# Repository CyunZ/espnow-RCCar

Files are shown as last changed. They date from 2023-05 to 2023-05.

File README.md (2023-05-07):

# espnow-RCCar
用espnow通讯的遥控车

### 额外物料
ESP32开发板 2个  
MG996R舵机 1个  
130高扭矩电机（附赠8齿齿轮） 1个  
蓝丁胶  
按钮 4个  
686ZZ轴承（6*13*5） 至少4只  
TLP281光耦模块 1个  
L298N电机驱动模块 1个  
DCDC模块 若干 （3.3V给单片机供电，5V给舵机、电机供电 ，可以拆废旧充电宝的模块代替）  
18650电池+电池盒 若干（1个DCDC模块至少需要2节电池，充电宝模块只需要1节）  
M2螺丝 若干（固定开发板用，可以用蓝丁胶代替）  
M3螺丝+螺母 若干  
洞洞板、排针、排母（非必须，减少杜邦线的使用，简洁一点而已）  
杜邦线 若干  

### 视频地址
https://www.bilibili.com/video/BV1cz4y1a7o8

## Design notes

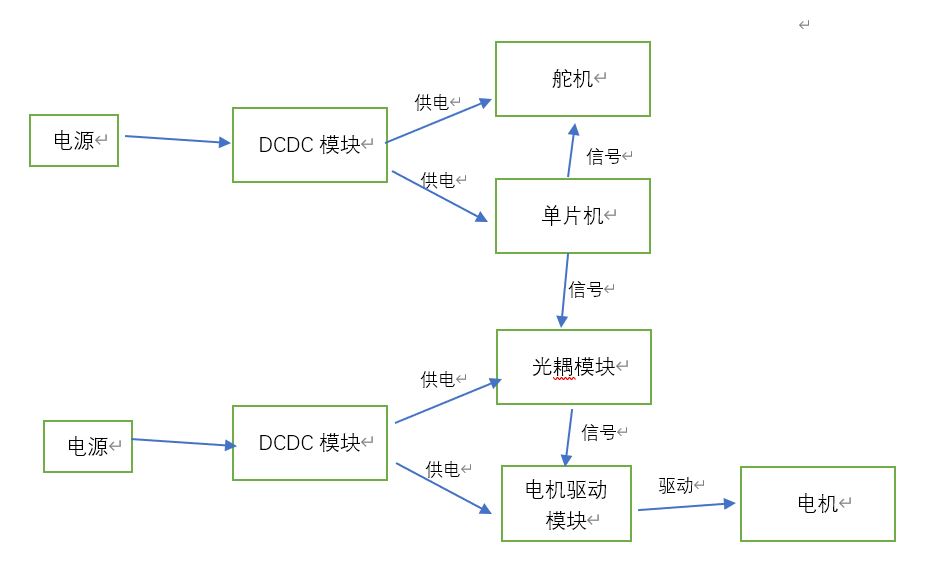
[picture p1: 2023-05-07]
接线示意图.JPG

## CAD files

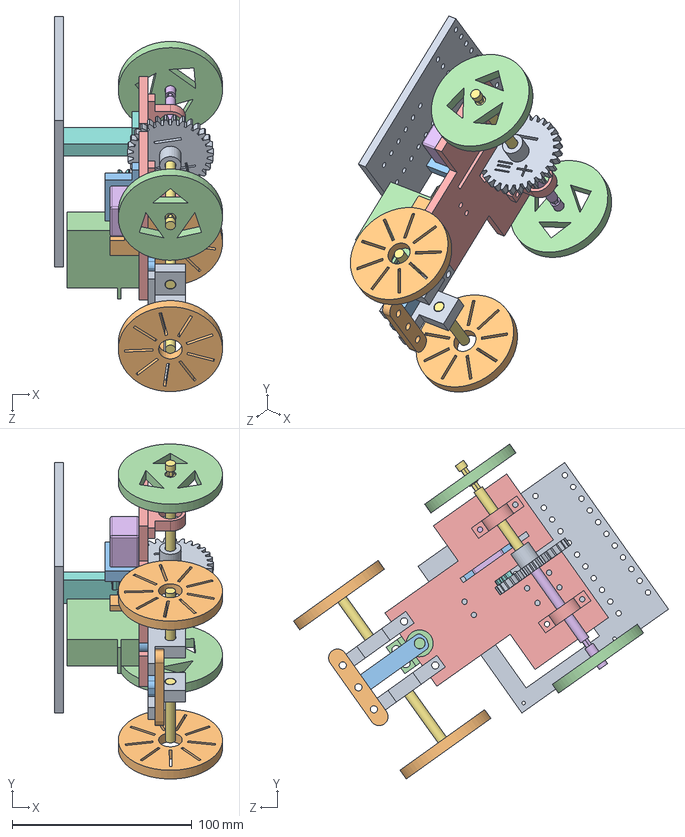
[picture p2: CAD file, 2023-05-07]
model/装配体2.SLDASM
93.5 x 186.4 x 208.7 mm
前连接杆2 x 2
最前杆
前连接转动杆
MG966R舵机
车身
电机
前轮轴 x 2
电机齿轮1.5模8齿
传动齿轮30齿1.5模
前轮2 x 2
电机扣
后轮2 x 2
轴承支架2 x 2
传动杆右2
传动杆左2
主板架
主板架上层
舵机架

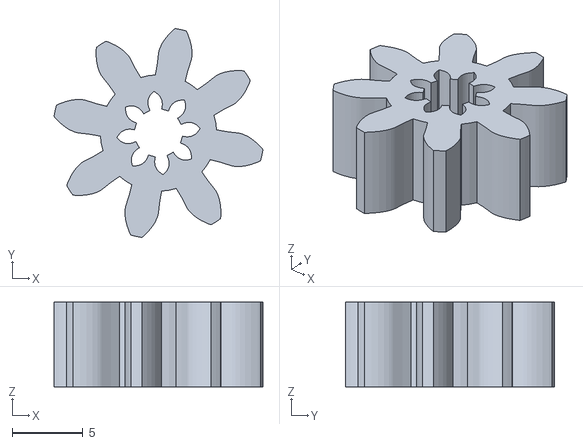
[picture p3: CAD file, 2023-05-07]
model/stl/电机齿轮.STL
14.8 x 14.8 x 6.00

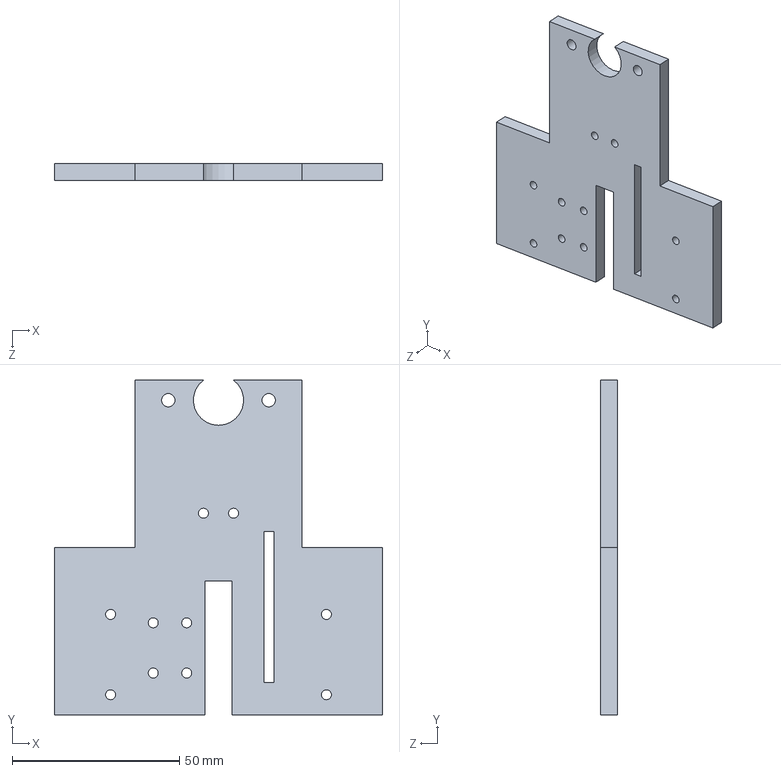
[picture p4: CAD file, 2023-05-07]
model/车身.SLDPRT
98.0 x 100.0 x 5.00 mm

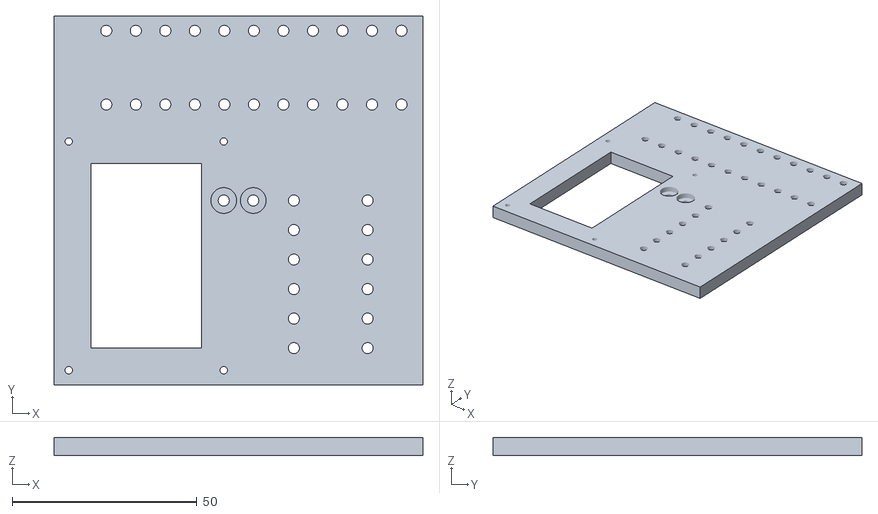
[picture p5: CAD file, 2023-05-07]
model/stl/主机架上层.STL
100.0 x 100.0 x 5.00

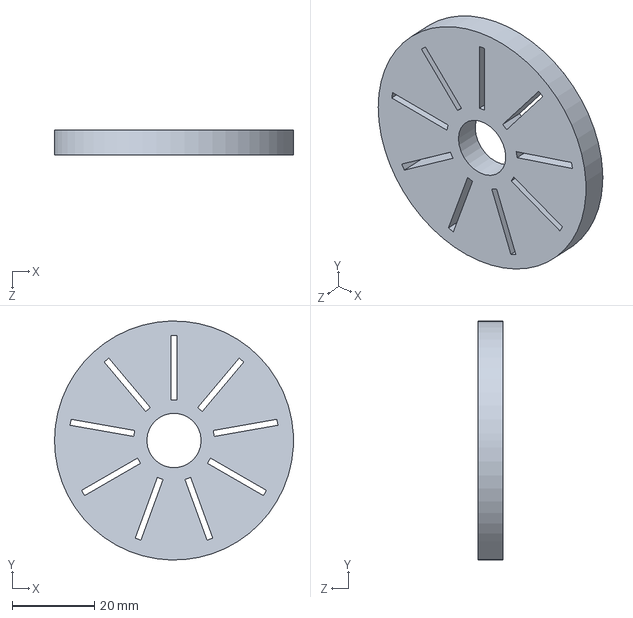
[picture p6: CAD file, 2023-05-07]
model/前轮2.SLDPRT
58.0 x 58.0 x 6.00 mm

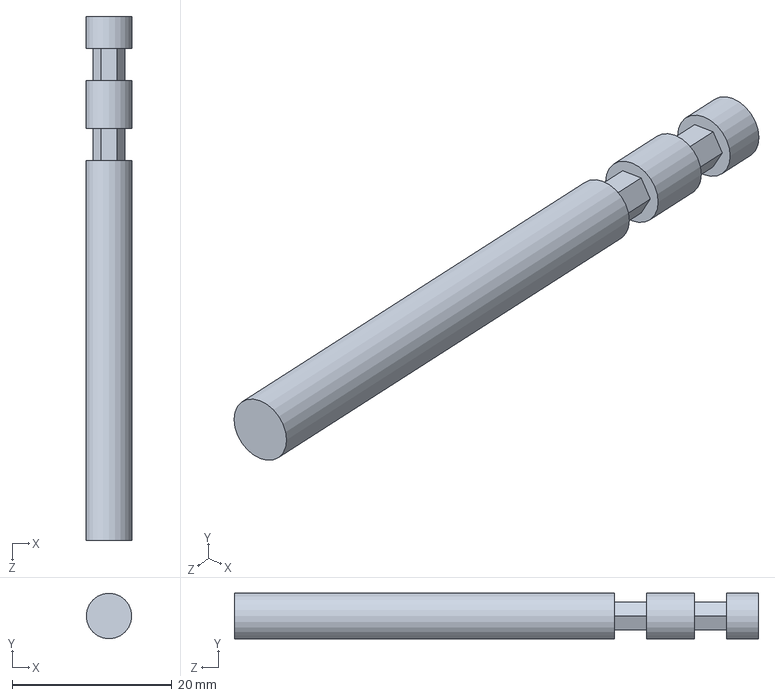
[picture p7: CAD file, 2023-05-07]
model/传动杆左2.SLDPRT
5.70 x 5.70 x 65.6 mm

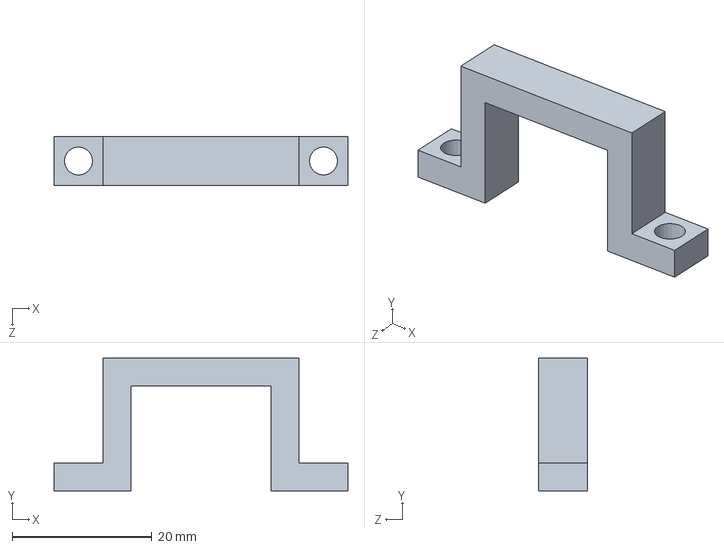
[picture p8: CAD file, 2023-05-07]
model/电机扣.SLDPRT
42.0 x 19.0 x 7.00 mm

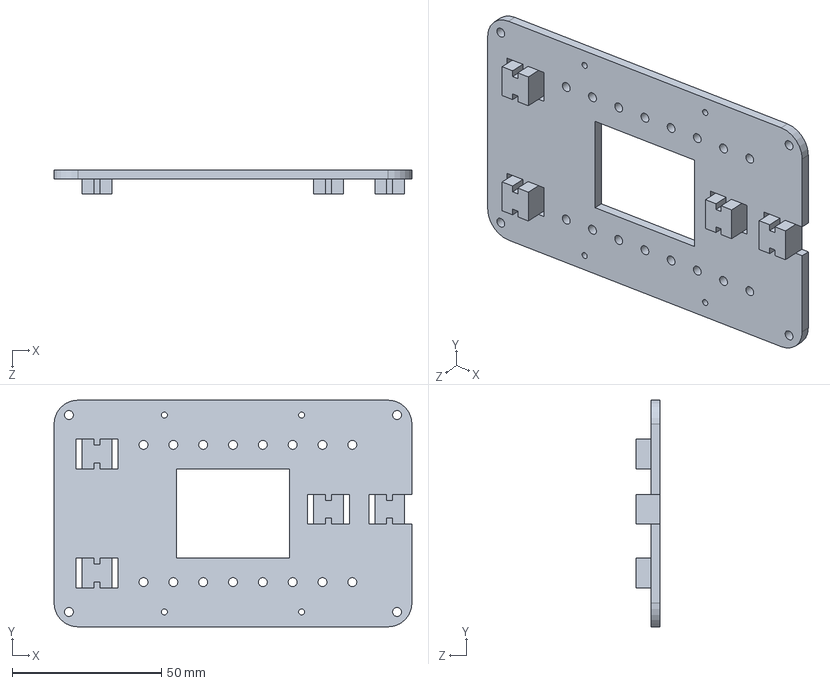
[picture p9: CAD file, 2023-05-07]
model/遥控器底壳.SLDPRT
120.0 x 76.0 x 8.00 mm

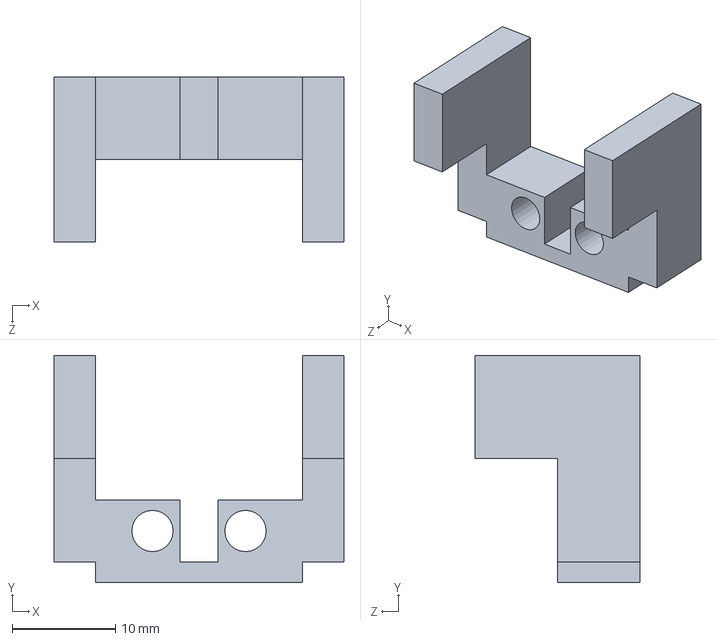
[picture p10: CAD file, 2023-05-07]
model/舵机架.SLDPRT
28.1 x 22.0 x 16.0 mm

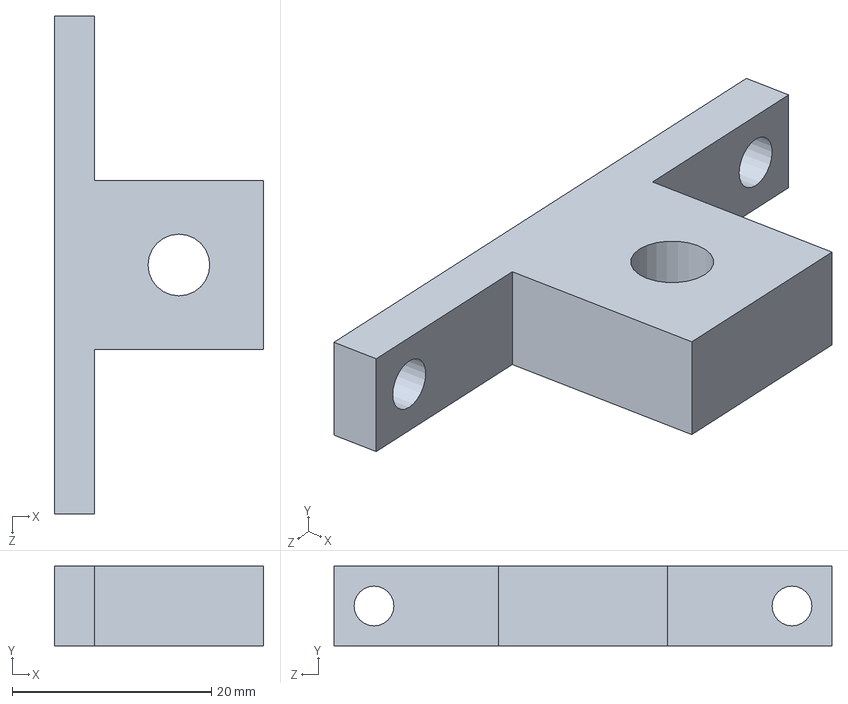
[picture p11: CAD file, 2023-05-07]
model/前连接杆2.SLDPRT
21.0 x 8.00 x 50.0 mm

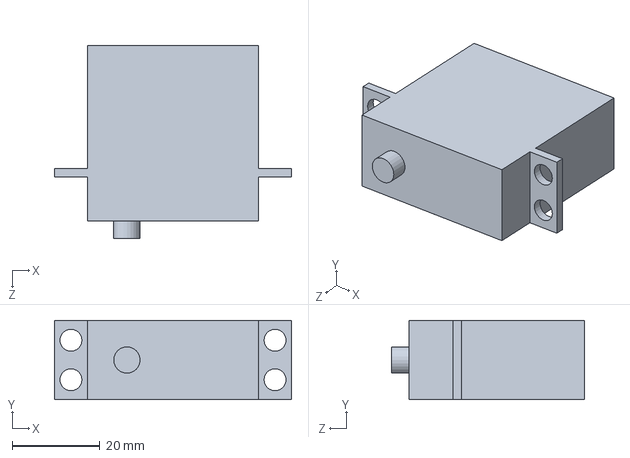
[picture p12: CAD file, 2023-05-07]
model/MG966R舵机.SLDPRT
54.0 x 18.0 x 44.0 mm

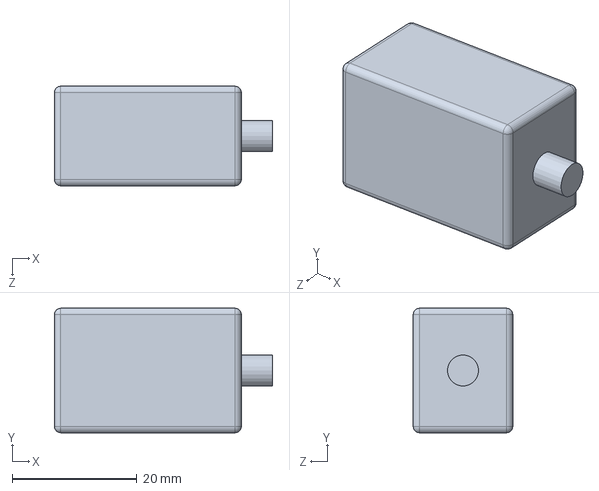
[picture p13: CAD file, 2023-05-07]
model/电机.SLDPRT
35.0 x 20.0 x 16.0 mm

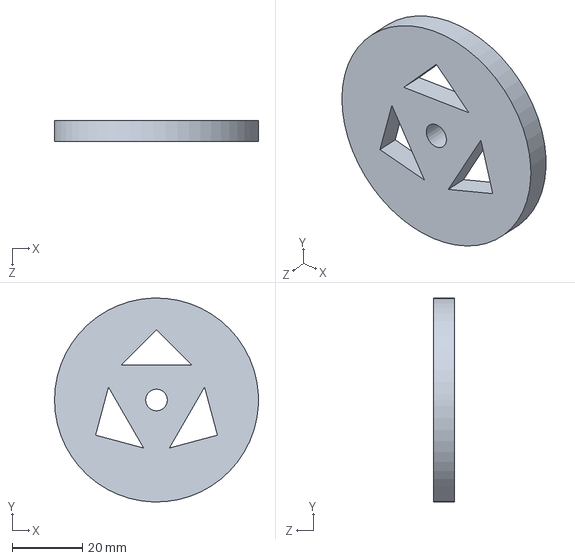
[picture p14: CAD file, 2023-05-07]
model/后轮2.SLDPRT
58.0 x 58.0 x 6.00 mm

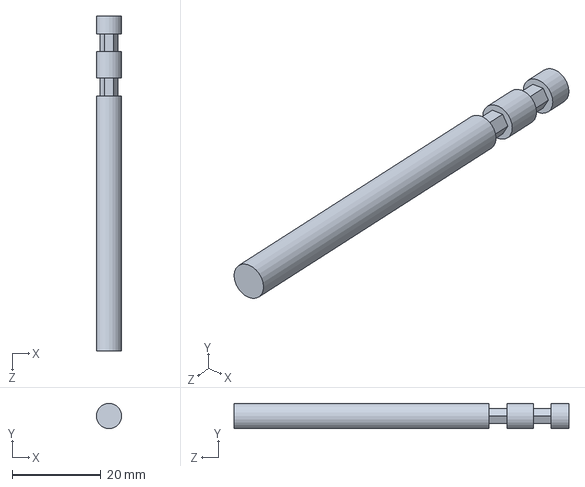
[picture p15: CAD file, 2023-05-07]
model/传动杆右2.SLDPRT
5.70 x 5.70 x 75.4 mm

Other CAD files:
model/电机齿轮1.5模8齿.SLDPRT
model/轴承支架2.SLDPRT
model/前轮轴.SLDPRT
model/前连接转动杆.SLDPRT
model/stl/主板架.STL
model/stl/传动杆右2.STL
model/stl/传动杆左2.STL
model/stl/传动齿轮30齿1.5模.STL
model/stl/前轮2.STL
model/stl/前轮轴.STL
model/stl/前连接杆2.STL
model/stl/前连接转动杆.STL
model/stl/后轮2.STL
model/stl/最前杆.STL
model/stl/电机扣.STL
model/stl/舵机架.STL
model/stl/车身.STL
model/stl/轴承支架2.STL
model/stl/遥控器底壳.STL
model/主板架.SLDPRT
model/主板架上层.SLDPRT
model/传动齿轮30齿1.5模.SLDPRT
model/最前杆.SLDPRT

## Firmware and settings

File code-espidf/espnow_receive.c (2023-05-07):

/* ESPNOW Example

   This example code is in the Public Domain (or CC0 licensed, at your option.)

   Unless required by applicable law or agreed to in writing, this
   software is distributed on an "AS IS" BASIS, WITHOUT WARRANTIES OR
   CONDITIONS OF ANY KIND, either express or implied.
*/

/*
   This example shows how to use ESPNOW.
   Prepare two device, one for sending ESPNOW data and another for receiving
   ESPNOW data.
*/
#include <stdlib.h>
#include <time.h>
#include <string.h>
#include <assert.h>
#include "freertos/FreeRTOS.h"
#include "freertos/semphr.h"
#include "freertos/timers.h"
#include "nvs_flash.h"
#include "esp_random.h"
#include "esp_event.h"
#include "esp_netif.h"
#include "esp_wifi.h"
#include "esp_log.h"
#include "esp_mac.h"
#include "esp_now.h"
#include "esp_crc.h"
#include "espnow_example.h"
#include "driver/gpio.h"
#include "driver/ledc.h"

#define ESPNOW_MAXDELAY 512

static const char *TAG = "espnow_example";

static uint8_t broadcast_mac[ESP_NOW_ETH_ALEN] = {0xFF, 0xFF, 0xFF, 0xFF, 0xFF, 0xFF};

//电机信号引脚
#define output_motor1 18
#define output_motor2 19

//舵机信号引脚
#define LEDC_OUTPUT_IO (33)  
#define LEDC_TIMER LEDC_TIMER_0
#define LEDC_MODE LEDC_LOW_SPEED_MODE
#define LEDC_CHANNEL LEDC_CHANNEL_0
#define LEDC_DUTY_RES LEDC_TIMER_10_BIT // 10位分辨率
#define LEDC_FREQUENCY (50)

// 占空比
// #define LEDC_DUTY_LEFT 26  //1023*0.025
#define LEDC_DUTY_LEFT 52   // 1023*0.05
#define LEDC_DUTY_MIDDLE 75 // 1023*0.075
#define LEDC_DUTY_RIGHT 102 // 1023*0.1
// #define LEDC_DUTY_RIGHT 127  //1023*0.125

static QueueHandle_t msgQ_UD;
static QueueHandle_t msgQ_LR;

/* WiFi should start before using ESPNOW */
static void example_wifi_init(void)
{
    ESP_ERROR_CHECK(esp_netif_init());
    ESP_ERROR_CHECK(esp_event_loop_create_default());
    wifi_init_config_t cfg = WIFI_INIT_CONFIG_DEFAULT();
    ESP_ERROR_CHECK(esp_wifi_init(&cfg));
    ESP_ERROR_CHECK(esp_wifi_set_storage(WIFI_STORAGE_RAM));
    ESP_ERROR_CHECK(esp_wifi_set_mode(ESPNOW_WIFI_MODE));
    ESP_ERROR_CHECK(esp_wifi_start());

#if CONFIG_ESPNOW_ENABLE_LONG_RANGE
    ESP_ERROR_CHECK(esp_wifi_set_protocol(ESPNOW_WIFI_IF, WIFI_PROTOCOL_11B | WIFI_PROTOCOL_11G | WIFI_PROTOCOL_11N | WIFI_PROTOCOL_LR));
#endif
}

static void recv_cb(const esp_now_recv_info_t *recv_info, const uint8_t *data, int len)
{

    char msg = (char)data[0];
    uint8_t *mac_addr = recv_info->src_addr;

    if (mac_addr == NULL || data == NULL || len <= 0)
    {
        ESP_LOGE(TAG, "Receive cb arg error");
        return;
    }
    printf("get msg:%c\n", msg);
    switch (msg)
    {
    case 'U': // 前
    case 'D': // 后
        if (xQueueSend(msgQ_UD, &msg, 0) != pdTRUE)
        {
            ESP_LOGW(TAG, "Send receive queue fail");
        }
        break;
    case 'L': // 左
    case 'R': // 右
        if (xQueueSend(msgQ_LR, &msg, 0) != pdTRUE)
        {
            ESP_LOGW(TAG, "Send receive queue fail");
        }
        break;
    }
}

/**
 * 驱动马达任务
 */
void driveTask_UD(void *pvParameter)
{
    char msg = 0;
    BaseType_t xStatus;
    while (1)
    {
        xStatus = xQueueReceive(msgQ_UD, &msg, 0);
        if (pdPASS == xStatus)
        {
            // printf("get msg:%c\n", msg);
            switch (msg)
            {
            case 'U': // 前
                gpio_set_level(output_motor1, 0);
                gpio_set_level(output_motor2, 1);
                break;
            case 'D': // 后
                gpio_set_level(output_motor1, 1);
                gpio_set_level(output_motor2, 0);
                break;
            }
        }
        else
        {
            // 无信息，停止
            gpio_set_level(output_motor1, 0);
            gpio_set_level(output_motor2, 0);
        }
        // 根据实际测试调整接受间隔
        vTaskDelay(100 / portTICK_PERIOD_MS);
    }
}

/**
 * 驱动舵机任务
 */
void driveTask_LR(void *pvParameter)
{
    char msg = 0;
    BaseType_t xStatus;
    while (1)
    {
        xStatus = xQueueReceive(msgQ_LR, &msg, 0);
        if (pdPASS == xStatus)
        {
            // printf("get msg:%c\n", msg);
            switch (msg)
            {
            case 'L': // 左
                ledc_set_duty(LEDC_MODE, LEDC_CHANNEL, LEDC_DUTY_LEFT);
                ledc_update_duty(LEDC_MODE, LEDC_CHANNEL);
                break;
            case 'R': // 右
                ledc_set_duty(LEDC_MODE, LEDC_CHANNEL, LEDC_DUTY_RIGHT);
                ledc_update_duty(LEDC_MODE, LEDC_CHANNEL);
                break;
            }
        }
        else
        {
            // 无信息，方向回中
            ledc_set_duty(LEDC_MODE, LEDC_CHANNEL, LEDC_DUTY_MIDDLE);
            ledc_update_duty(LEDC_MODE, LEDC_CHANNEL);
            // ESP_LOGE(TAG, "no msg");
        }
        // 根据实际测试调整接受间隔
        vTaskDelay(100 / portTICK_PERIOD_MS);
    }
}


static esp_err_t example_espnow_init(void)
{
    /* Initialize ESPNOW and register sending and receiving callback function. */
    ESP_ERROR_CHECK(esp_now_init());
    ESP_ERROR_CHECK(esp_now_register_recv_cb(recv_cb));
#if CONFIG_ESP_WIFI_STA_DISCONNECTED_PM_ENABLE
    ESP_ERROR_CHECK(esp_now_set_wake_window(65535));
#endif

    /* Add broadcast peer information to peer list. */
    esp_now_peer_info_t *peer = malloc(sizeof(esp_now_peer_info_t));
    if (peer == NULL)
    {
        ESP_LOGE(TAG, "Malloc peer information fail");
        return ESP_FAIL;
    }
    memset(peer, 0, sizeof(esp_now_peer_info_t));
    peer->channel = CONFIG_ESPNOW_CHANNEL;
    peer->ifidx = ESPNOW_WIFI_IF;
    peer->encrypt = false;
    memcpy(peer->peer_addr, broadcast_mac, ESP_NOW_ETH_ALEN);
    ESP_ERROR_CHECK(esp_now_add_peer(peer));
    free(peer);

    return ESP_OK;
}

void gpio_init()
{
    gpio_config_t io_conf = {};
    io_conf.intr_type = GPIO_INTR_DISABLE;
    io_conf.mode = GPIO_MODE_OUTPUT;
    io_conf.pin_bit_mask = ((1ULL << output_motor1) | (1ULL << output_motor2));
    io_conf.pull_down_en = 0;
    io_conf.pull_up_en = 0;
    gpio_config(&io_conf);
}

void ledc_init(void)
{
    // Prepare and then apply the LEDC PWM timer configuration
    ledc_timer_config_t ledc_timer = {
        .speed_mode = LEDC_MODE,
        .timer_num = LEDC_TIMER,
        .duty_resolution = LEDC_DUTY_RES,
        .freq_hz = LEDC_FREQUENCY, // Set output frequency at 5 kHz
        .clk_cfg = LEDC_AUTO_CLK};
    ESP_ERROR_CHECK(ledc_timer_config(&ledc_timer));

    // Prepare and then apply the LEDC PWM channel configuration
    ledc_channel_config_t ledc_channel = {
        .speed_mode = LEDC_MODE,
        .channel = LEDC_CHANNEL,
        .timer_sel = LEDC_TIMER,
        .intr_type = LEDC_INTR_DISABLE,
        .gpio_num = LEDC_OUTPUT_IO,
        .duty = 0, // Set duty to 0%
        .hpoint = 0};
    ESP_ERROR_CHECK(ledc_channel_config(&ledc_channel));
}

void app_main(void)
{
    msgQ_UD = xQueueCreate(2, sizeof(char));
    msgQ_LR = xQueueCreate(2, sizeof(char));
    if (msgQ_UD == NULL || msgQ_LR == NULL)
    {
        ESP_LOGE(TAG, "Create Queue fail");
        return;
    }
    gpio_init();
    ESP_LOGE(TAG, "gpio_init");
    ledc_init();
    ESP_LOGE(TAG, "ledc_init");
    // Initialize NVS
    esp_err_t ret = nvs_flash_init();
    if (ret == ESP_ERR_NVS_NO_FREE_PAGES || ret == ESP_ERR_NVS_NEW_VERSION_FOUND)
    {
        ESP_ERROR_CHECK(nvs_flash_erase());
        ret = nvs_flash_init();
    }
    ESP_ERROR_CHECK(ret);

    example_wifi_init();
    example_espnow_init();
    ESP_LOGE(TAG, "example_espnow_init");
    xTaskCreate(driveTask_UD, "driveTask_UD", 1024 * 5, (void *)msgQ_UD, 4, NULL);
    xTaskCreate(driveTask_LR, "driveTask_LR", 1024 * 5, (void *)msgQ_LR, 4, NULL);
}

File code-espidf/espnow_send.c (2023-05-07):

#include <stdlib.h>
#include <time.h>
#include <string.h>
#include <assert.h>
#include "freertos/FreeRTOS.h"
#include "freertos/semphr.h"
#include "freertos/timers.h"
#include "nvs_flash.h"
#include "esp_random.h"
#include "esp_event.h"
#include "esp_netif.h"
#include "esp_wifi.h"
#include "esp_log.h"
#include "esp_mac.h"
#include "esp_now.h"
#include "esp_crc.h"
#include "espnow_example.h"
#include "driver/gpio.h"

#define ESPNOW_MAXDELAY 512

static const char *TAG = "espnow_send";

static uint8_t broadcast_mac[ESP_NOW_ETH_ALEN] = {0xFF, 0xFF, 0xFF, 0xFF, 0xFF, 0xFF};

#define input_up  25
#define input_down  26
#define input_left  18
#define input_right  19

/* WiFi should start before using ESPNOW */
static void example_wifi_init(void)
{
    ESP_ERROR_CHECK(esp_netif_init());
    ESP_ERROR_CHECK(esp_event_loop_create_default());
    wifi_init_config_t cfg = WIFI_INIT_CONFIG_DEFAULT();
    ESP_ERROR_CHECK(esp_wifi_init(&cfg));
    ESP_ERROR_CHECK(esp_wifi_set_storage(WIFI_STORAGE_RAM));
    ESP_ERROR_CHECK(esp_wifi_set_mode(ESPNOW_WIFI_MODE));
    ESP_ERROR_CHECK(esp_wifi_start());

#if CONFIG_ESPNOW_ENABLE_LONG_RANGE
    ESP_ERROR_CHECK(esp_wifi_set_protocol(ESPNOW_WIFI_IF, WIFI_PROTOCOL_11B | WIFI_PROTOCOL_11G | WIFI_PROTOCOL_11N | WIFI_PROTOCOL_LR));
#endif
}

/**
 * 发送回调
 **/
static void sendCb(const uint8_t *mac_addr, esp_now_send_status_t status)
{
    if (ESP_NOW_SEND_SUCCESS == status)
    {
        ESP_LOGI(TAG, "esp_now send success");
    }
    else
    {
        ESP_LOGE(TAG, "esp_now send fail");
    }
}

static esp_err_t example_espnow_init(void)
{
    ESP_ERROR_CHECK(esp_now_init());
    ESP_ERROR_CHECK(esp_now_register_send_cb(sendCb));
#if CONFIG_ESP_WIFI_STA_DISCONNECTED_PM_ENABLE
    ESP_ERROR_CHECK(esp_now_set_wake_window(65535));
#endif

    /* Add broadcast peer information to peer list. */
    esp_now_peer_info_t *peer = malloc(sizeof(esp_now_peer_info_t));
    if (peer == NULL)
    {
        ESP_LOGE(TAG, "Malloc peer information fail");
        return ESP_FAIL;
    }
    memset(peer, 0, sizeof(esp_now_peer_info_t));
    peer->channel = CONFIG_ESPNOW_CHANNEL;
    peer->ifidx = ESPNOW_WIFI_IF;
    peer->encrypt = false;
    memcpy(peer->peer_addr, broadcast_mac, ESP_NOW_ETH_ALEN);
    ESP_ERROR_CHECK(esp_now_add_peer(peer));
    free(peer);

    return ESP_OK;
}

/**
 *  发送前后
 * */
static void sendTask_UD(void *pvParameter)
{
    QueueHandle_t msgQ_UD = (QueueHandle_t)pvParameter;
    BaseType_t xStatus;
    char msg = 0;
    while (1)
    {
        // 一直等待消息，一有就发送
        xStatus = xQueueReceive(msgQ_UD, &msg, portMAX_DELAY);
        if (pdPASS == xStatus)
        {
            ESP_LOGI(TAG, "queue receive success");
            if (esp_now_send(broadcast_mac, (uint8_t *)&msg, sizeof(char)) != ESP_OK)
            {
                ESP_LOGE(TAG, "esp_now Send error");
            }
            printf("try to send '%c' ",msg);
        }
        else
        {
            ESP_LOGE(TAG, "queue receive fail");
        }
    }
}

static void sendTask_LR(void *pvParameter)
{
    QueueHandle_t msgQ_LR = (QueueHandle_t)pvParameter;
    BaseType_t xStatus;
    char msg = 0;
    while (1)
    {
        // 一直等待消息，一有就发送
        xStatus = xQueueReceive(msgQ_LR, &msg, portMAX_DELAY);
        if (pdPASS == xStatus)
        {
            ESP_LOGI(TAG, "queue receive success");
            if (esp_now_send(broadcast_mac, (uint8_t *)&msg, sizeof(char)) != ESP_OK)
            {
                ESP_LOGE(TAG, "esp_now Send error");
            }
            printf("try to send '%c' ",msg);
        }
        else
        {
            ESP_LOGE(TAG, "queue receive fail");
        }
    }
}

/**
 * 按钮按下
*/
void UD_Task(void *pvParameter)
{
    QueueHandle_t msgQ_UD = (QueueHandle_t)pvParameter;
    // BaseType_t xStatus;
    char msg = 'U';
    int up, down;
    while (1)
    {
        // 获取按键输入
        up = gpio_get_level(input_up);       // 前
        down = gpio_get_level(input_down);   // 后
        // 发送前后，同时按下，前优先
        if (up == 0)
        {
            msg = 'U';
            xQueueSend(msgQ_UD, &msg, 0);
        }
        else if (down == 0)
        {
            msg = 'D';
            xQueueSend(msgQ_UD, &msg, 0);
        }

        vTaskDelay(100 / portTICK_PERIOD_MS);
    }
}

/**
 * 左右按下
*/
void LR_Task(void *pvParameter)
{
    QueueHandle_t msgQ_LR = (QueueHandle_t)pvParameter;
    // BaseType_t xStatus;
    char msg = 'L';
    int  left, right;
    while (1)
    {
        // 获取按键输入
        left = gpio_get_level(input_left);   // 左
        right = gpio_get_level(input_right); // 右

        // 发送左右，同时按下，左优先
        if (left == 0)
        {
            msg = 'L';
            xQueueSend(msgQ_LR, &msg, 0);
        }
        else if (right == 0)
        {
            msg = 'R';
            xQueueSend(msgQ_LR, &msg, 0);
        }
        vTaskDelay(100 / portTICK_PERIOD_MS);
    }
}


void gpio_init()
{
    gpio_config_t io_conf = {};
    io_conf.intr_type = GPIO_INTR_DISABLE;
    io_conf.mode = GPIO_MODE_INPUT;
    io_conf.pin_bit_mask = ((1ULL << input_up) | (1ULL << input_down) | (1ULL << input_left) | (1ULL << input_right));
    io_conf.pull_down_en = 0;
    io_conf.pull_up_en = 1;
    gpio_config(&io_conf);
}

void app_main(void)
{

    QueueHandle_t msgQ_UD = xQueueCreate(1, sizeof(char));
    QueueHandle_t msgQ_LR = xQueueCreate(1, sizeof(char));
    if (msgQ_UD == NULL || msgQ_LR ==  NULL)
    {
        ESP_LOGE(TAG, "Create mutex fail");
        return;
    }

    gpio_init();

    // Initialize NVS
    esp_err_t ret = nvs_flash_init();
    if (ret == ESP_ERR_NVS_NO_FREE_PAGES || ret == ESP_ERR_NVS_NEW_VERSION_FOUND)
    {
        ESP_ERROR_CHECK(nvs_flash_erase());
        ret = nvs_flash_init();
    }
    ESP_ERROR_CHECK(ret);

    example_wifi_init();
    example_espnow_init();

    xTaskCreate(sendTask_UD, "sendTask_UD", 2048, (void *)msgQ_UD, 4, NULL);
    xTaskCreate(sendTask_LR, "sendTask_LR", 2048, (void *)msgQ_LR, 4, NULL);
    xTaskCreate(UD_Task, "UD_Task", 2048, (void *)msgQ_UD, 4, NULL);
    xTaskCreate(LR_Task, "LR_Task", 2048, (void *)msgQ_LR, 4, NULL);
}
